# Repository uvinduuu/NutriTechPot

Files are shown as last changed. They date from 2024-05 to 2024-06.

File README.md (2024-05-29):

# NutriTechPot

**EN - 1190 ENGINEERING DESIGN PROJECT**

---

## Table of Contents
1. [Problem Description and Motivation](#problem-description-and-motivation)
2. [Product Idea Validation](#product-idea-validation)
3. [Technical Feasibility](#technical-feasibility)
4. [Product Architecture](#product-architecture)
5. [Changes We Made](#changes-we-made)
6. [Designs](#designs)
7. [Marketing and Sales](#marketing-and-sales)
8. [Future Improvements](#future-improvements)
9. [Power Consumption and Battery Life](#power-consumption-and-battery-life)
10. [Project Budget](#project-budget)
11. [Contact](#contact)

---

## Problem Description and Motivation

### Problem Description
Many people struggle with keeping their plants alive due to inconsistent watering and inadequate sunlight. For busy individuals or those without a green thumb, this can be a frustrating and costly problem. Our project aims to address this issue by creating a smart plant pot that automatically waters plants when the soil moisture level is low to ensure optimal growing conditions. By providing a solution to this common problem, we hope to make plant care more accessible and enjoyable for everyone.

### Motivation
The motivation for selecting the smart plant pot project was driven by the growing trend of agriculture-based products in the world. With an increasing focus on sustainability and healthy living, more people are turning to plant care as a way to connect with nature and improve their indoor air quality. By creating a smart plant pot that automates watering, we aim to make plant care more accessible and enjoyable for everyone. Furthermore, with the rising interest in smart home technology, we believe that our product has the potential to tap into a large and growing market.

---

## Product Idea Validation
We conducted a survey among a randomly selected group of about 50 people to validate the product idea for our smart plant pot. The survey revealed that a majority of participants struggled with plant care due to inconsistent watering and providing fertilization. Most people stated that they liked gardening but didn't have enough time to look after plants, and they often forgot to water them. Over 70% of respondents expressed interest in using a smart plant pot that automatically waters their plants. Participants also identified features such as automatic watering and real-time monitoring as desirable in a smart plant pot. Based on the survey results, we believe that our smart plant pot has promising market potential and addresses a common pain point among plant enthusiasts.

---

## Technical Feasibility
The product is designed to automatically water plants when the soil moisture level is low for optimal plant growth. To achieve this, we will use hardware components such as the Atmega328p microcontroller, capacitive soil moisture sensor, DC water pump, and a water level detector. All necessary components are readily available. Software requirements include the Arduino IDE for programming the microcontroller, Android Studio for app development, Altium Designer for PCB design, and Solidworks for enclosure design. We plan to hire professionals for PCB printing and 3D printing. The necessary resources, including soldering equipment, are available.

---

## Product Architecture

- **Power Supply**
- **Soil Moisture Sensor**
- **Atmega 328p Microcontroller**
- **DC Water Pump**
- **Water Level Sensor**
- **Bluetooth Module**
- **NutriTech App**

The NutriTech application tracks the water level in the tank, alerts the user when a refill is needed, and constantly monitors the soil moisture level, presenting the data in an easily understandable format to the user.

---

## Changes We Made
Initially, we planned to use a Wi-Fi module (ESP 8266) for communication between the chip and the NutriTech Pot application. However, we encountered significant challenges with this approach, such as needing to modify the code every time the pot was moved to a different Wi-Fi network. We switched to using a Bluetooth module (HC-05), which offers higher accuracy and a more user-friendly experience. This change enhanced the overall functionality and user experience of the NutriTech Pot application.

---

## Designs

### Schematic Diagram
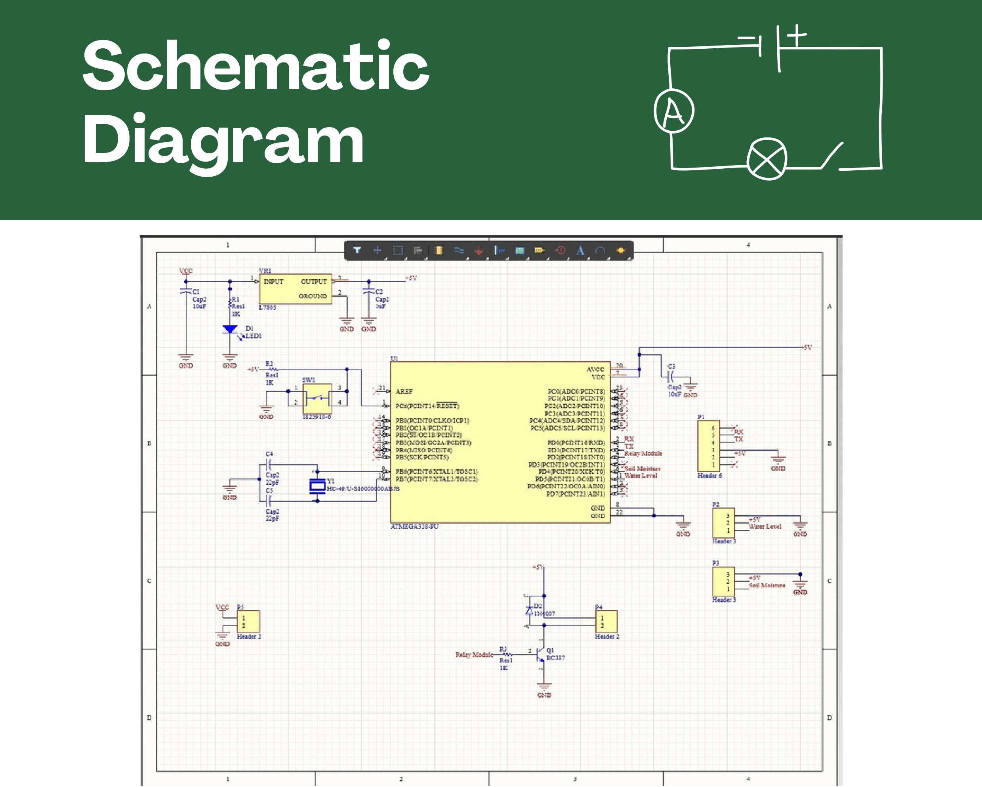
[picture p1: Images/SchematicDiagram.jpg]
Schematic Diagram


### NutriTech Pot App
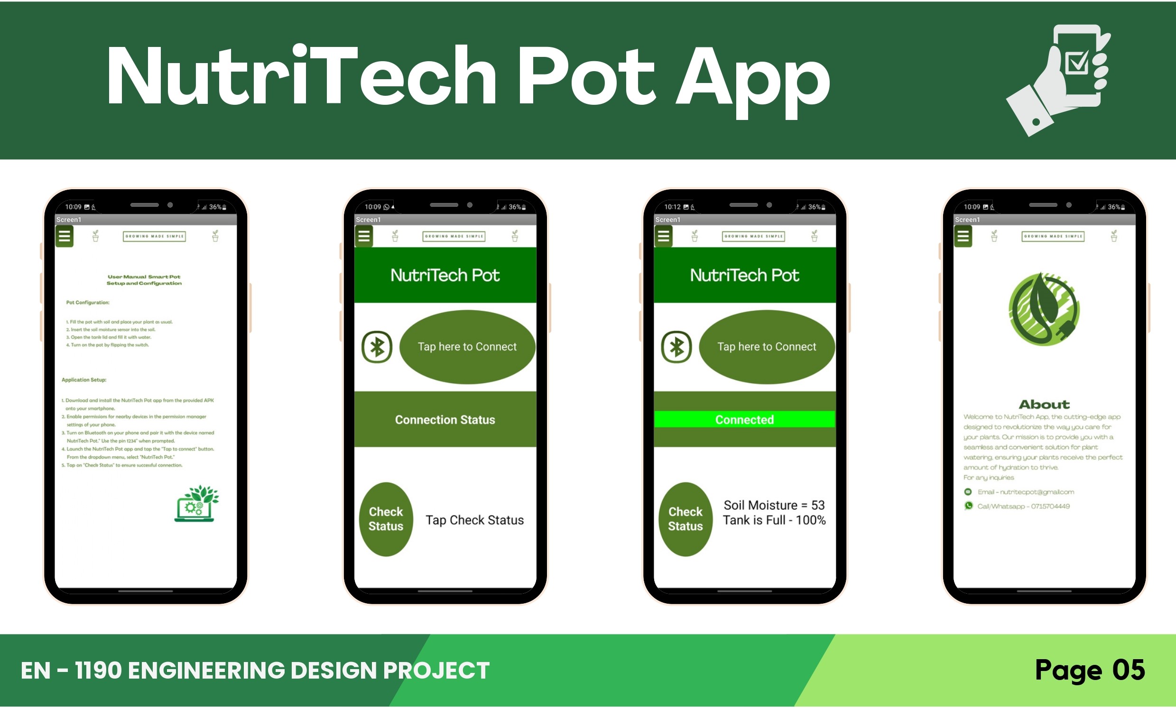
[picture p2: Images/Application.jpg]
NutriTech Pot App


### Altium Design
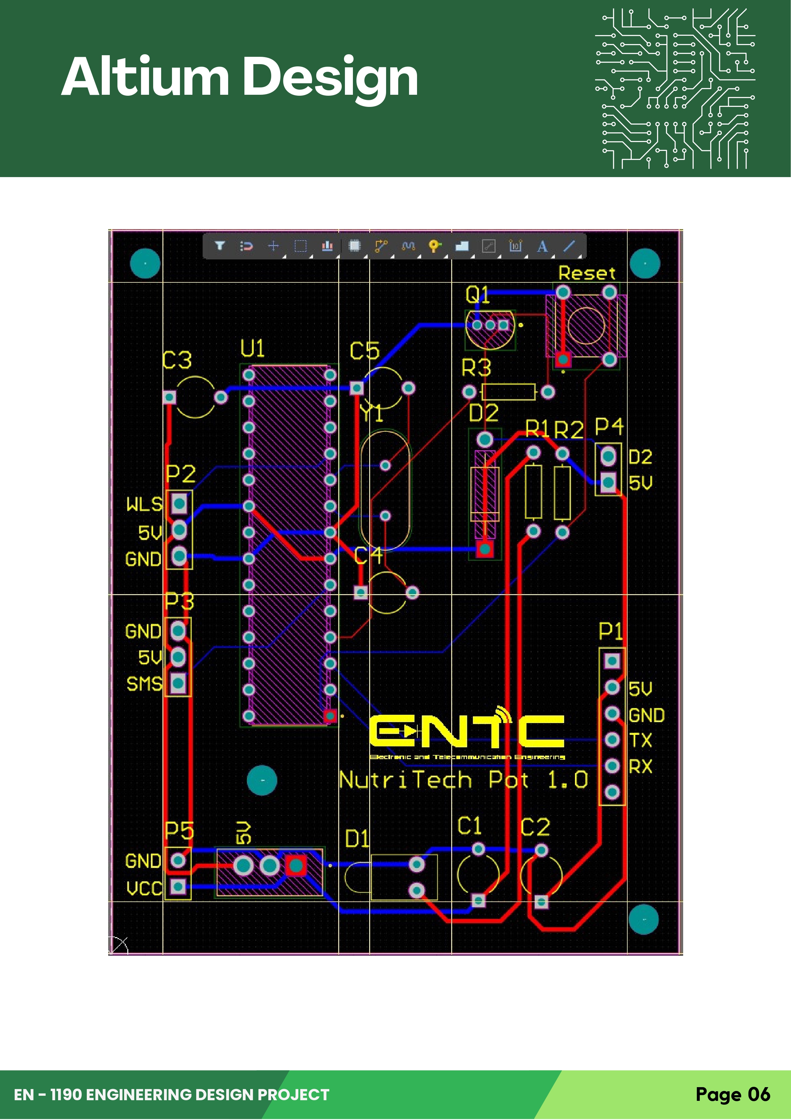
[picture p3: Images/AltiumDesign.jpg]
Altium Design


### Final Enclosure
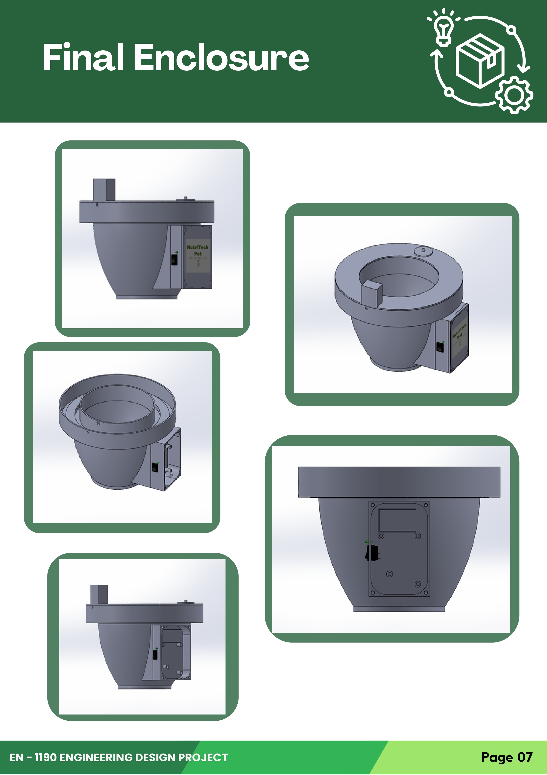
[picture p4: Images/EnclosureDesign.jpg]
Final Enclosure


---

## Marketing and Sales

### Competitive Forces
The market is new and growing, with evolving competition. Product quality, pricing, support, and marketing affect competitive forces. Intensified competition and tech advancements require staying ahead.

### Marketing Strategies
- **Social Media Marketing**
- **Influencer Marketing**
- **Email Marketing**
- **Content Marketing**

### Target Markets
Our project targets people who care about gardening and sustainability, especially those living in urban areas with limited outdoor space or who are too busy to take care of plants manually. We plan to market the product to them by emphasizing its convenience and benefits.

### Product Packaging
The product packaging will be made of recycled materials and have eco-friendly messaging and imagery. It will also be sturdy and protective to keep the product safe during transport.

### Warranty Terms
We offer a 6-month warranty period with a 10-month service period for the smart watering and fertilizing pot, covering any defects in materials or workmanship. The warranty period is clearly communicated to customers, and any necessary steps for claiming warranty are made easily accessible.

### After Sales Service
We provide clear instructions for cleaning and upkeep to ensure the product lasts for a long time. Additionally, we offer repair services for any damages or malfunctions that occur during the warranty and service period.

### Reuse/Recycle and Disposal
We encourage customers to reuse and recycle the product when it is no longer needed. The product is designed to be easily disassembled and recyclable at the end of its life cycle. We also plan to offer recycling programs or incentives for customers who choose to recycle the product.

### Sales Channels
- **Online Marketplaces:** Daraz, Ikman.lk, eBay
- **E-Commerce Website**
- **Retail Stores:** Collaborations with retail stores

---

## Future Improvements

### Bottlenecks of the Initial Plan
We initially powered the circuit using a 9V battery with a voltage regulator (L7805). However, the motor's high power draw caused the circuit to power down intermittently.

### Solution
We implemented two separate voltage regulators (L7805) – one for the Atmega chip's power supply and another for the DC water pump. We replaced the 9V battery with two rechargeable Li-ion batteries (3.7V Li-Fe 18650) for improved performance and stability. This ensured a consistent power supply to both the chip and the motor.

---

## Power Consumption and Battery Life
Through testing with a DC power supply, we measured the circuit's current draw when the motor was on at 160-170 mA and when the motor was off at 68-75 mA. We calculated an approximate power consumption of 1730mAh, providing nearly two and a half days of battery life on a single recharge. We used two rechargeable Li-ion batteries (3.7V Li-Fe 18650) connected in series due to the rapid discharge of the 9V battery.

---

## Project Budget

| Component | Qty | Unit Price (LKR) | Total Price (LKR) |
| --- | --- | --- | --- |
| Atmega328p Microcontroller | 1 | 1400.00 | 1400.00 |
| Capacitive Soil Moisture sensor | 1 | 400.00 | 400.00 |
| HC-05 Bluetooth Module | 1 | 1100.00 | 1100.00 |
| DC Water Pump | 1 | 380.00 | 380.00 |
| Li-ion batteries (3.7V Li-Fe 18650)| 2 | 600.00 | 1200.00 |
| Water Level Detector | 1 | 110.00 | 110.00 |
| 16MHz Crystal Oscillator | 1 | 40.00 | 40.00 |
| Resistors (1 kOhm - 1, 10 kOhm - 1)| 2 | 3.00 | 6.00 |
| BC 337 npn Transistor | 1 | 5.00 | 5.00 |
| IN 4007 Diode | 1 | 5.00 | 5.00 |
| Push Button Switch | 1 | 30.00 | 30.00 |
| Voltage Regulator | 2 | 50.00 | 100.00 |
| Capacitors | 5 | 5.00 | 25.00 |
| Connectors | 6 | 20.00 | 120.00 |
| LED | 2 | 15.00 | 30.00 |
| **Total** | | | **4951.00** |

### Total Production Cost
- Rs 3000 (For multiple product manufacturing)
- PCB Printing and 3D Printing - Rs 200 (per unit)
- Market Price - Rs 3600
- Manufacturing Quantities - 50 units

---
## Contact

For more information about the NutriTech Pot, contact us:

- Email: uvindukodikara@gmail.com
---

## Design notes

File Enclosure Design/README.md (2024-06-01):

# NutriTech Pot Enclosure

Welcome to the NutriTech Pot Enclosure repository! This repository contains the design files for the enclosure of the NutriTech Pot, a smart plant pot with an automatic watering system. Currently, we have designed and printed the PCB housing box, which will be the first step towards the full product.



## Features

- **Simple Box Design**: The enclosure is a straightforward, easy-to-assemble box with a lid.
- **PCB Mounting**: The PCB can be securely fixed inside the box using M3 screws.
- **Battery Compartment**: The enclosure has space to fit a 9V battery.
- **Power Control**: Equipped with a rocker switch to turn the power on and off.
- **Power Indicator**: Includes an LED to indicate the power status.

## Dimensions

- **Box Size**: 120 mm x 70 mm

## Usage

1. **Print the Box**: Use the provided SolidWorks files to 3D print the enclosure.
2. **Mount the PCB**: Fix the PCB inside the box using M3 screws.
3. **Install the Battery**: Place a 9V battery in the designated compartment.
4. **Connect the Rocker Switch and LED**: Wire the rocker switch and LED as indicated to control and show the power status.

## Future Plans

Originally designed with an inbuilt water tank, the NutriTech Pot will eventually include a complete system for automatic watering. This initial enclosure is just for the PCB and power components.

WhatsApp Image 2024-05-16 at 10 39 33_1c1a7363

## Contact

For any questions or inquiries, please contact [mihiruth@gmail.com](mailto:mihiruth@gmail.com).

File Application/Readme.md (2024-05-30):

# Nutritech Pot Application

Nutritech Pot is a smart watering system designed to help you maintain optimal soil moisture levels for your plants. This application, built using MIT App Inventor, connects to your Nutritech Pot via Bluetooth and provides real-time monitoring and alerts.

## Features

- **Bluetooth Connectivity**: Connect to your Nutritech Pot using Bluetooth to start monitoring.
- **Real-time Soil Moisture Level**: View the current soil moisture level as a percentage.
- **Water Tank Level**: Check the water tank level as a percentage.
- **Refill Alerts**: Receive notifications when it's time to refill the water tank.

## Getting Started

1. **Connect via Bluetooth**: Open the app and connect to your Nutritech Pot device via Bluetooth.
2. **Monitor Levels**: Once connected, the app will display real-time soil moisture and water tank levels.
3. **Refill Alerts**: The app will alert you when the water tank needs refilling.

## Requirements

- An Android device with Bluetooth capability.
- Nutritech Pot hardware.

## Installation

1. Download the Nutritech Pot APK from the release section.
2. Install the APK on your Android device.
3. Open the app and pair it with your Nutritech Pot device via Bluetooth.

## Usage

1. Open the app and navigate to the Bluetooth connection screen.
2. Select your Nutritech Pot device from the list of available devices.
3. Monitor the soil moisture level and water tank level displayed on the main screen.
4. Refill the water tank when you receive an alert.

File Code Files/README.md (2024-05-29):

# Soil Moisture and Water Level Monitoring System

## Features:

- **Soil Moisture Measurement**: The `measureSoilMoisture` function reads the soil moisture level and maps it to a percentage.
- **Water Level Measurement**: The `measureWaterLevel` function reads the water level and turns on an LED if the level is below a certain threshold.
- **Water Pump Control**: The `controlWaterPump` function turns the water pump on or off based on soil moisture and water level.
- **Bluetooth Communication**: The `sendBluetoothData` function sends the soil moisture and water level data to a mobile application via an HC-05 Bluetooth module.

## Setup Instructions:

1. **Hardware Connections**:
   - Connect the soil moisture sensor to the analog pin A3.
   - Connect the water pump to pin A5.
   - Connect the water level sensor to analog pin A1.
   - Connect an LED to pin 13 for low water level indication.
   - Connect the HC-05 Bluetooth module to pins 2 (RX) and 3 (TX).

2. **Calibration Values**:
   - Adjust the `OpenAirReading` and `WaterReading` values in the code based on your soil moisture sensor's calibration.
   - Adjust the `WATER_LEVEL_THRESHOLD` value based on your water level sensor's calibration.

3. **Thresholds**:
   - Set the desired soil moisture threshold (`MOISTURE_THRESHOLD`) to control the water pump.

4. **Software Configuration**:
   - Ensure the correct pins are defined in the code.
   - Upload the provided Arduino sketch to your Arduino board.

5. **Bluetooth Communication**:
   - Pair the HC-05 Bluetooth module with your mobile application.
   - The soil moisture and water level data will be sent as a percentage to the connected mobile application.
   - If the water level is low, the message will include a refill alert.

## Notes:

- Adjust pin numbers, calibration values, and thresholds according to your specific setup and sensor calibration.
- Ensure proper power supply connections for the sensors and modules.
- The delay between measurements and data transmission is set to 1 second. Adjust this as needed for your application.

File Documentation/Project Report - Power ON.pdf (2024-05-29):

## EN - 1190 ENGINEERING DESIGN PROJECT

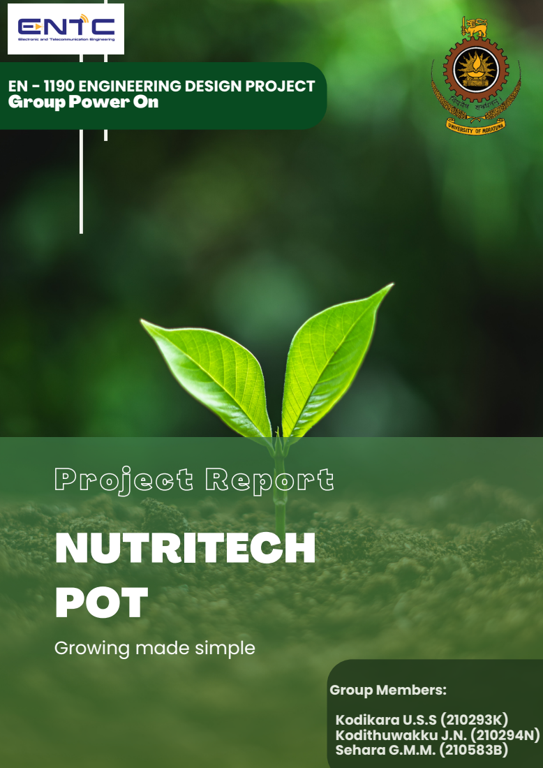
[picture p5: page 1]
Group Members:; Kodikara U.S.S (210293K) Kodithuwakku J.N. (210294N) Sehara G.M.M. (210583B); NUTRITECH POT; Project Report

Group Power On

Growing made simple

# Table of Contents

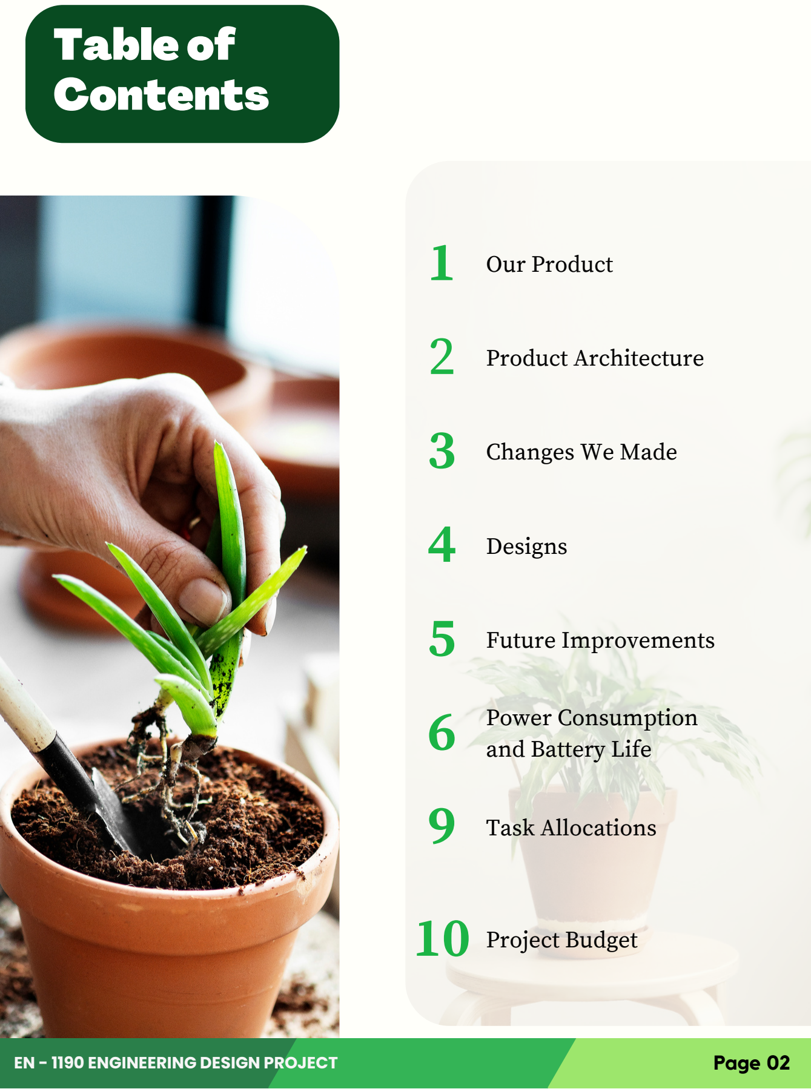
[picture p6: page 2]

## 1 Our Product

## 2 Product Architecture

## 3 Changes We Made

## 4 Designs

## 5 Future Improvements

6

## Power Consumption and Battery Life

## 9 Task Allocations

## 10 Project Budget

EN - 1190 ENGINEERING DESIGN PROJECT | Page 02

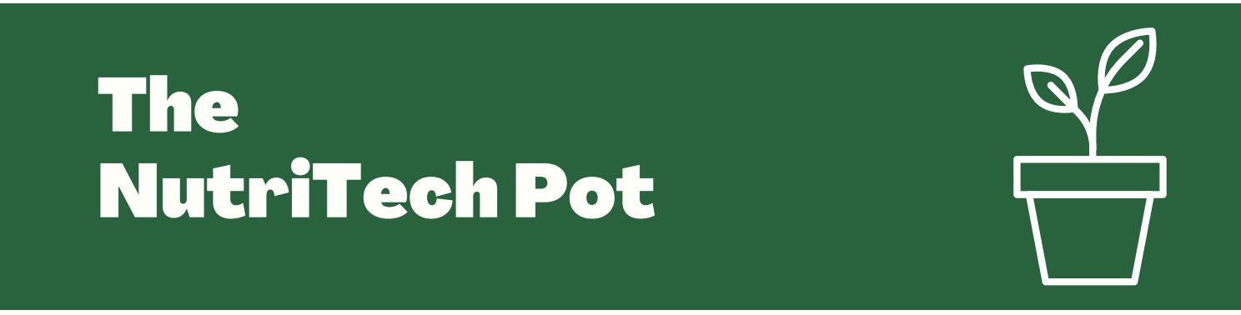
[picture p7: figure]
The NutriTech Pot
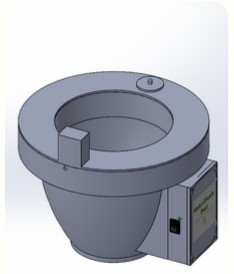
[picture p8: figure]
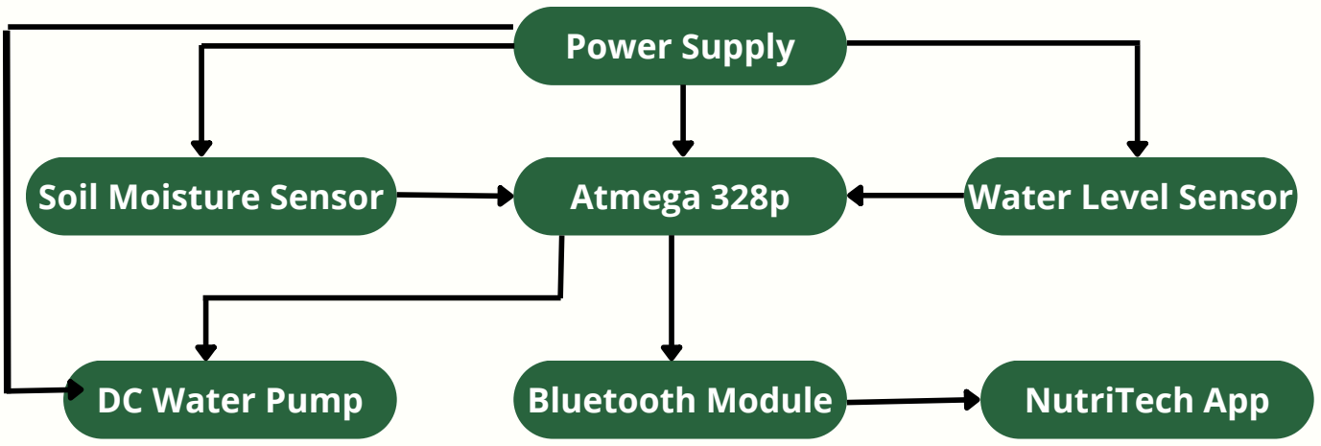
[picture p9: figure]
Power Supply; Soil Moisture Sensor; Atmega 328p; DC Water Pump; Water Level Sensor; Bluetooth Module; NutriTech App

EN - 1190 ENGINEERING DESIGN PROJECT | Page 03

The project aims to address the issues of plant watering by creating a smart plant pot that automatically waters plants when the soil moisture level is low to ensure optimal growing conditions.

The purpose of our product, the NutriTech pot, is to make gardening easier and more convenient for individuals who are interested in sustainable living but may not have access to outdoor gardening spaces or have busy lifestyles.
The pot is equipped with a soil moisture sensor and a water pump that automatically waters the plant when the soil moisture level is low. It also includes a water level detector that measures the water level in the tank and alerts the user when to add water.

## Product Architechture

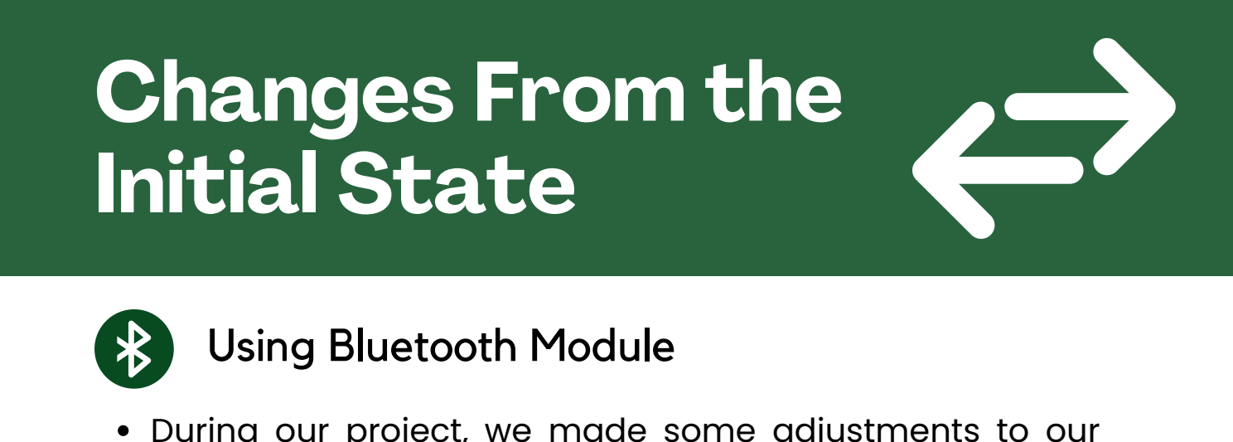
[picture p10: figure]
Studio Shodwe; Changes From the Initial State; Using Bluetooth Module
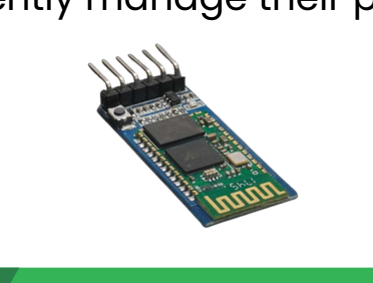
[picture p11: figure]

EN - 1190 ENGINEERING DESIGN PROJECT | Page 04

## During our project, we made some adjustments to our initial plan. Initially, we intended to employ a Wi-Fi module (esp 8266) for communication between the chip

and the NutriTech pot application.

## However, during the code development phase, we recognized a significant challenge with this approach. To

establish a connection between the app and the module,

## we needed to know the Network SSID and password of the Wi-Fi network which the module was meant to connect. This would have necessitated modifying the code every time the pot was moved to a different Wi-Fi

network, making it less practical for users.

## As a result, we sought an alternative solution and concluded that Bluetooth (HC-05) was a more suitable

option to establish the connection.

## Although Bluetooth has a shorter range compared to Wi-Fi, it offers higher accuracy and a more user-friendly experience. By using Bluetooth, we can seamlessly monitor the status of the pot and determine whether the tank requires a refill, as long as we are within a range of

approximately 10 meters from the pot.

This decision to switch to Bluetooth not only overcame the limitations of Wi-Fi but also enhanced the overall functionality and user experience of the NutriTech pot application. It allowed us to focus on delivering a more efficient and effective solution for our users, enabling them to conveniently manage their pot's watering needs

# Schematic Diagram

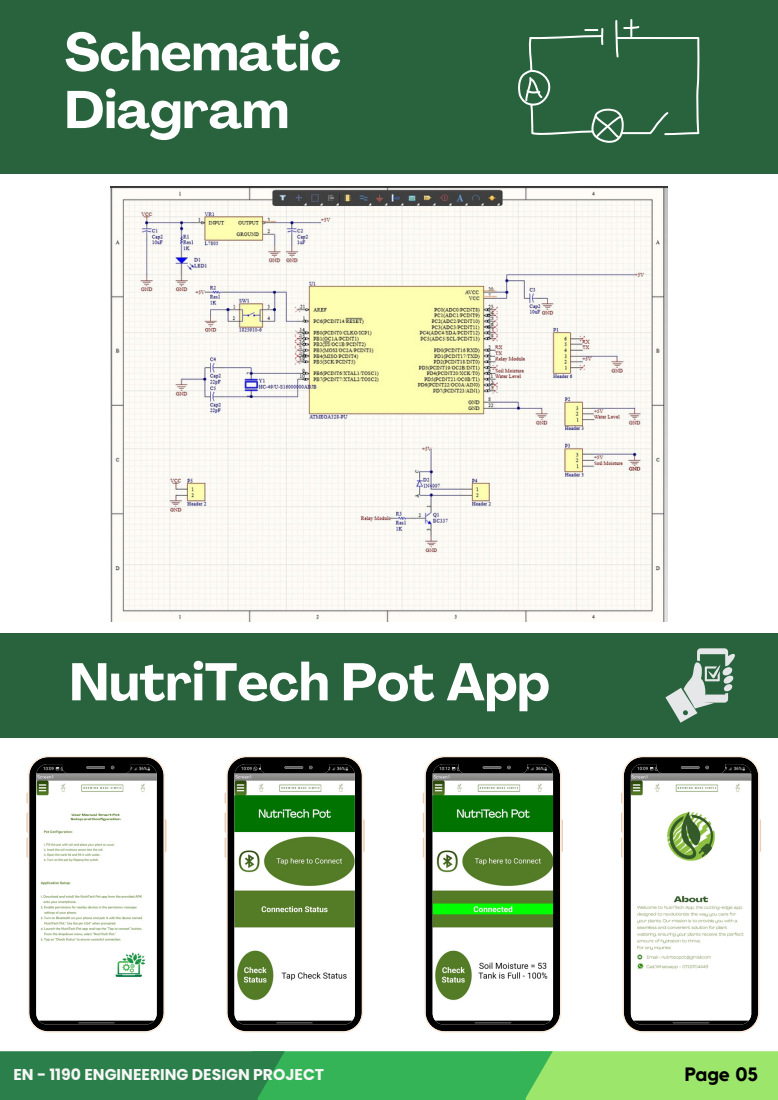
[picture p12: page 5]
Studio Shodwe; EN - 1190 ENGINEERING DESIGN PROJECT; Page 05

NutriTech Pot App

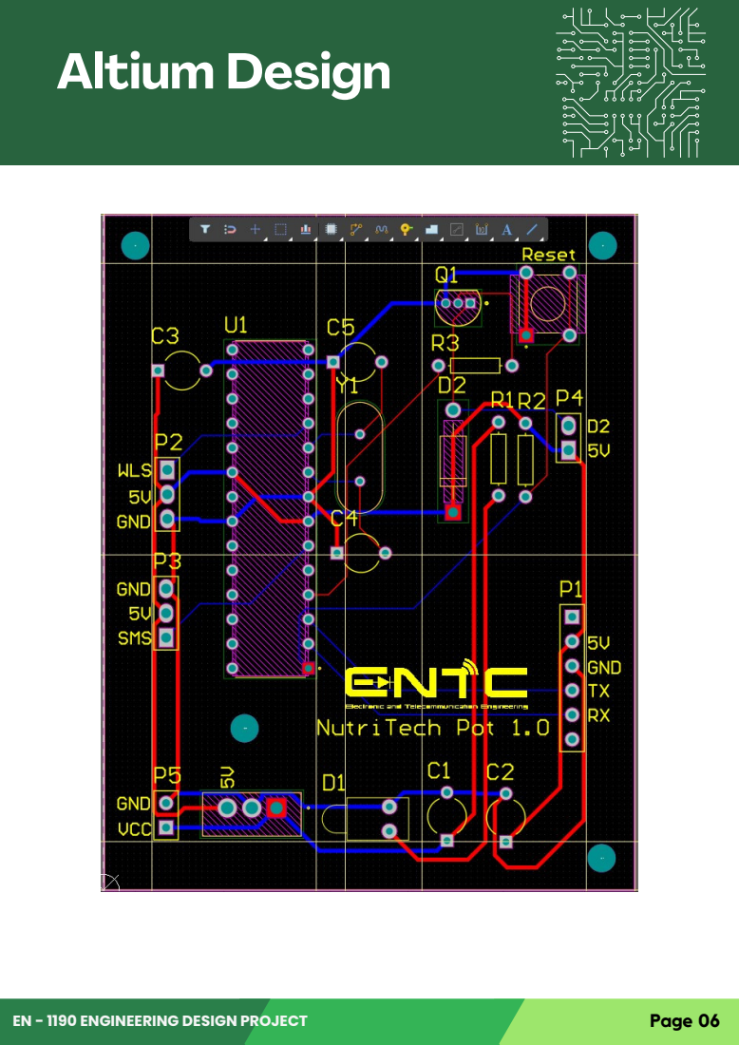
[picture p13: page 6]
AltiuSmtudio SDhodewesign; EN - 1190 ENGINEERING DESIGN PROJECT; Page 06

# FinalStEudionShcodwloe sure

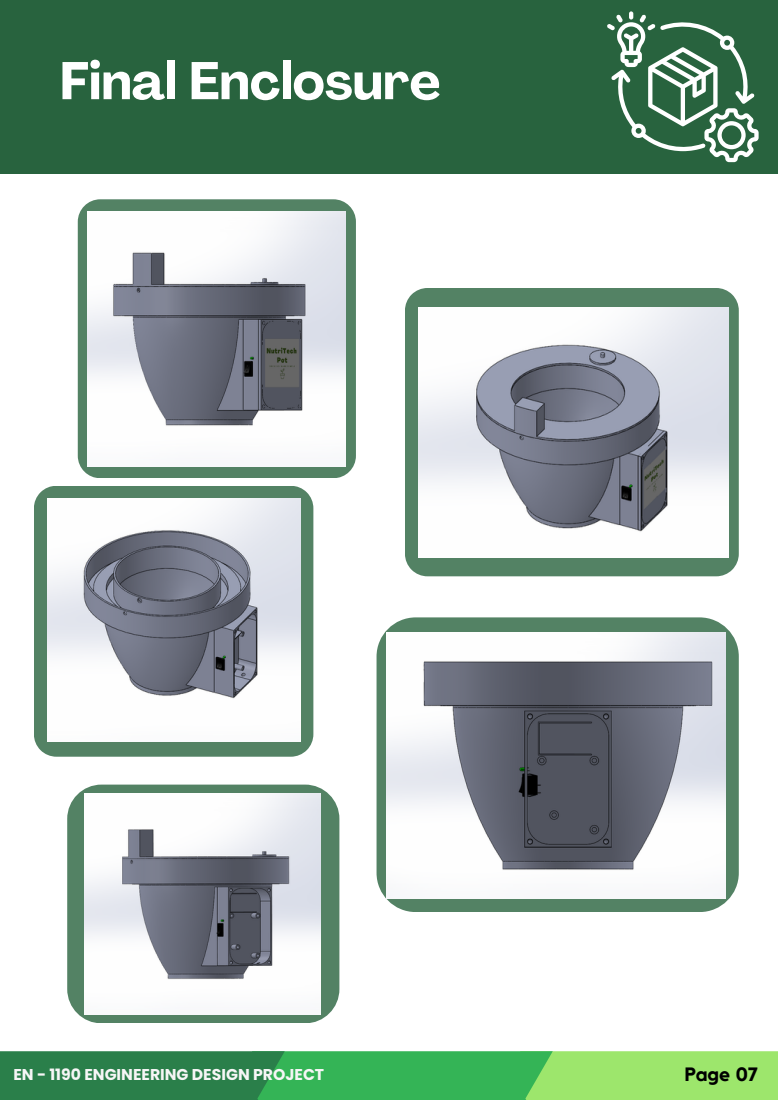
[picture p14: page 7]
EN - 1190 ENGINEERING DESIGN PROJECT; Page 07

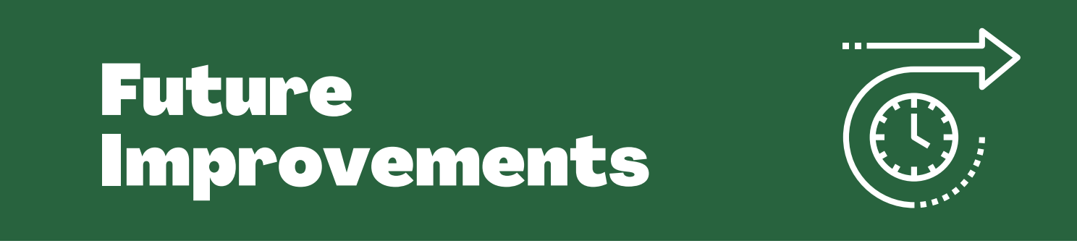
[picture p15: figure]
Future Improvements

B O T T L E N E C K S O F T H E I N I T I A L P L A N
In the project report, we initially planned to power the circuit using a 9V battery connected with a voltage regulator (L7805). However, during testing, we encountered a significant issue when the motor started to power up. The power LED began to blink, and the circuit powered down for a few seconds, repeating the same behavior.

We identified that the problem occurred because the motor drew a high amount of power from the circuit, which the power supply couldn't deliver. As a result, the voltage to the chip decreased, leading to the circuit's shutdown.

R E A S O N S

To address this issue, we devised a solution. We decided to implement two separate voltage regulators (L7805) – one for the atmega chip's power supply and another for the DC water pump. Additionally, we replaced the 9V battery with two rechargeable Li-ion batteries (3.7V Li-Fe 18650) as the new power supply for improved performance and stability. This modification allowed us to ensure a consistent power supply to both the chip and the motor, resolving the previous problem.

S O L U T I O N

D E M O N S T R A T I O N
For the demonstration, we utilized an LED instead of the DC water pump since it draws less current and effectively showcases the functionality of our product. Unfortunately, we couldn't alter the power supply in this instance due to the constraints of the enclosure and PCB, which were designed for the previously planned circuit.

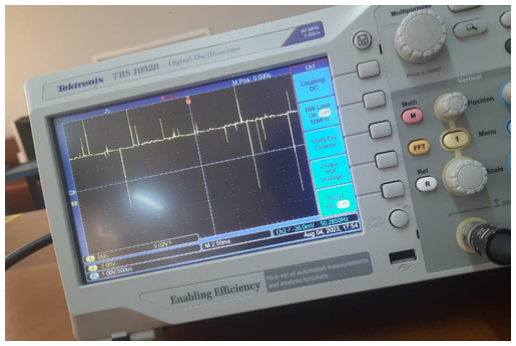
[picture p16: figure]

EN - 1190 ENGINEERING DESIGN PROJECT | Page 08 The photo shows an instance when the motor is connected to the circuit
with 9v battery.
| We can see a greater amount of
noise there

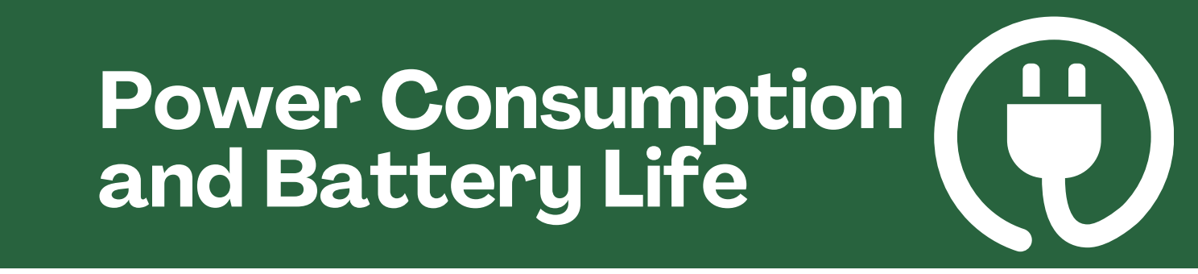
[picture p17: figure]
Power Consumption and Battery Life

EN - 1190 ENGINEERING DESIGN PROJECT | Page 09

Through testing with a DC power supply, we measured the circuit's current draw when the motor was on at 160-170 mA and when the motor was off at 68-75 mA.
Based on these observations, we calculated an approximate power consumption of 1730mAh, which would provide nearly two and a half days of battery life on a single recharge.
This estimation assumes a normal day with the
motor | activated | five | times | for | 15
seconds each time.

## Using two rechargeable Li-ion batteries (3.7V Li-Fe 18650) as the power supply

Due to the rapid discharge of the 9V battery, we
decided to use two 3.7V batteries connected in
series.

## Battery Life and Power Consumption

# Task Allocation

Kodikara K.S.S. - Microcontroller Programming and Mobile App Kodithuwakku J.N. - Altium and PCB Design
Sehara G.M.M. - Solidworks and Enclosure Design

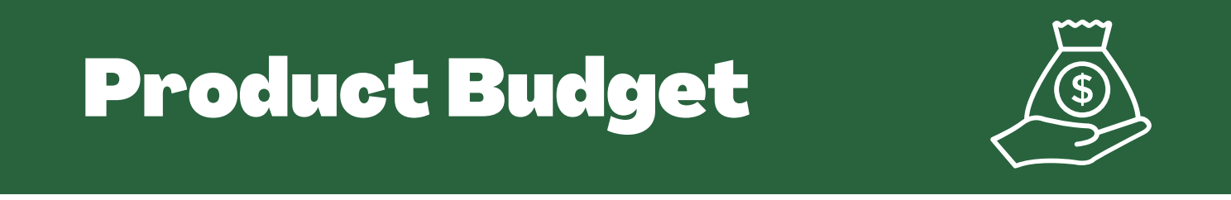
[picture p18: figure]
Product Budget

Component | Qty | Unit Price (LKR) | Price (LKR)
atmega328p Micro Controller | 1 | 1400.00 | 1400.00
Capacitive Soil Moisture sensor(MD0247) | 1 | 400.00 | 400.00
HC-05 Bluetooth Module | 1 | 1100 | 1100.00
DC water pump(RB0031) | 1 | 380.00 | 380.00
Li-ion batteries (3.7V Li-Fe 18650) | 2 | 600.00 | 1200.00
Water Level Detector(MD0207) | 1 | 110.00 | 110.00
16MHz Crystal Oscillator | 1 | 40.00 | 40.00
Resistors (1 kOhm - 1, 10 kOhm - 1) | 2 | 3.00 | 6.00
BC 337 npn Transistor | 1 | 5.00 | 5.00
IN 4007 Diode | 1 | 5.00 | 5.00
Push Button Switch | 1 | 30.00 | 30.00
Voltage Regulator | 2 | 50 | 100.00
Capacitors (10 micro F - 1, 22 pF - 2) | 5 | 5.00 | 25.00
Connectors | 6 | 20.00 | 120.00
LED | 2 | 15.00 | 30.00
Total | | | 4951.00
Total production cost | - Rs 4800(For multiple Product manufacturing)
PCB Printing and Injection Molding - Rs 1000 (per one unit)
Market Price | - Rs 7000
Manufacturing Quantities | - 50
EN - 1190 ENGINEERING DESIGN PROJECT | Page 10

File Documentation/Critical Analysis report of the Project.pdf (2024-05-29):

Critical Analysis report of the Project

NutriTech Pot: Team PowerOn

Kodikara U. S. S. – 210293K

Kodithuwakku J. N. – 210294N

Sehara G. M. M. – 210583B

Introduction:

Gardening has become a popular hobby among people, but not everyone has the time or expertise to provide their plants with the necessary care. As a solution to this issue, a smart pot that can detect and regulate water and fertilizer levels as required to maintain the plant's health is proposed. The idea is based on the application of deductive, inductive, and abductive reasoning to arrive at a practical and useful solution. This proposal aims to refine the idea further, including extended analysis of its technical, economic, and environmental aspects.

Deductive Reasoning:

Deductive reasoning entails using general observations to arrive at a specific conclusion. In the context of the proposed smart pot, the general observation is that many individuals enjoy gardening but do not have the time or expertise to give their plants the attention they require. As a result, a smart pot that can detect and regulate water and fertilizer levels as needed is suggested as a solution. To achieve this, the smart pot will include sensors to detect moisture levels, sunlight exposure, and fertilizer levels. The sensors will then send this data to an app that will regulate the water and fertilizer levels to keep the plant healthy. The smart pot will be beneficial for people who want to enjoy gardening but have time constraints, ensuring that their plants are well-cared for without requiring regular attention.

Inductive Reasoning:

Inductive reasoning involves drawing broad conclusions from specific observations. The observation in this context is that many individuals desire to engage in gardening activities but lack the time to care for their plants consistently. The smart pot's development is based on this observation and aims to give users a convenient way to keep an eye on their plants' health and regulate their water and fertilizer levels. The smart pot will help users to engage in gardening activities, enhancing their living space and providing a therapeutic outlet while requiring minimal effort.

Abductive Reasoning:

Abductive reasoning entails combining observations and imaginative thinking to arrive at a tenable solution. In this context, the observation is that many people are unable to care for their plants consistently due to time constraints. The solution proposed is a smart pot that can detect and regulate water and fertilizer levels as needed. The smart pot will also include a small tank filled with fertilizer liquid, which will release the necessary amount of fertilizer when the sensor detects a deficiency. The smart pot will also include a sunlight-measuring function to ensure that the plant is getting the necessary amount of light. The combination of these features will enable individuals to engage in gardening activities with minimal effort and ensure that their plants receive the care they require.

Extended Analysis:

The proposed smart pot has the potential to provide numerous benefits, including time-saving, convenience, and enhanced plant health. However, its efficacy, affordability, and environmental impact must be analyzed before its widespread use can be recommended.

Technical Analysis:

The technical analysis of the smart pot will include an assessment of its sensors, the app's effectiveness, and the device's durability. The sensors must be accurate and reliable to ensure that the plant receives the necessary care. The app must be user-friendly, and its data must be updated in real-time to provide timely information. The device must be durable and able to withstand the elements, ensuring that it can be used indoors or outdoors.

Economic Analysis:

The economic analysis will involve an assessment of the smart pot's cost-effectiveness, market demand, and profitability. The cost of the device must be affordable, allowing a wide range of individuals to access it. The market demand for the device must be sufficient to ensure its viability, and the device must be profitable to ensure its long-term sustainability.

Environmental Analysis:

The environmental impact of the smart pot must also be considered. The device must be made from environmentally sustainable materials, and its energy usage must be minimized to reduce its carbon footprint. The device must also be recyclable

Future Directions:

We plan to enhance the system by adding a charging module, which will eliminate the need for users to change batteries. Additionally, we will offer customized pots with unique designs for people in need.

Objectives: Our objectives for this project are as follows:

1. Incorporate a charging module into the pot to eliminate the need for users to change batteries.
2. Create customized pots with unique designs to meet the needs of different plants and customers.

Methodology: To achieve our objectives, we will follow the following methodology:

1. Integrate a charging module into the pot, which will use renewable energy sources to charge the battery and eliminate the need for users to change batteries.
2. Create customized pots with unique designs for different plants and customers, using 3D printing technology to produce them efficiently.

Expected Results: We expect the following results from our project:

1. A charging module that eliminates the need for users to change batteries and reduces maintenance costs.
2. Customized pots with unique designs that meet the needs of different plants and customers, providing an aesthetically pleasing and functional solution for indoor plant care.

Conclusion:

Our project aims to create a smart watering and fertilizing pot that is both functional and aesthetically pleasing, using sensors, microcontrollers, and 3D printing technology. By incorporating a charging module and offering customized designs, we aim to provide a user-friendly and sustainable solution for indoor plant care. We believe that this project has the potential to improve people's lives by promoting indoor plant growth, while also reducing the environmental impact of disposable batteries.

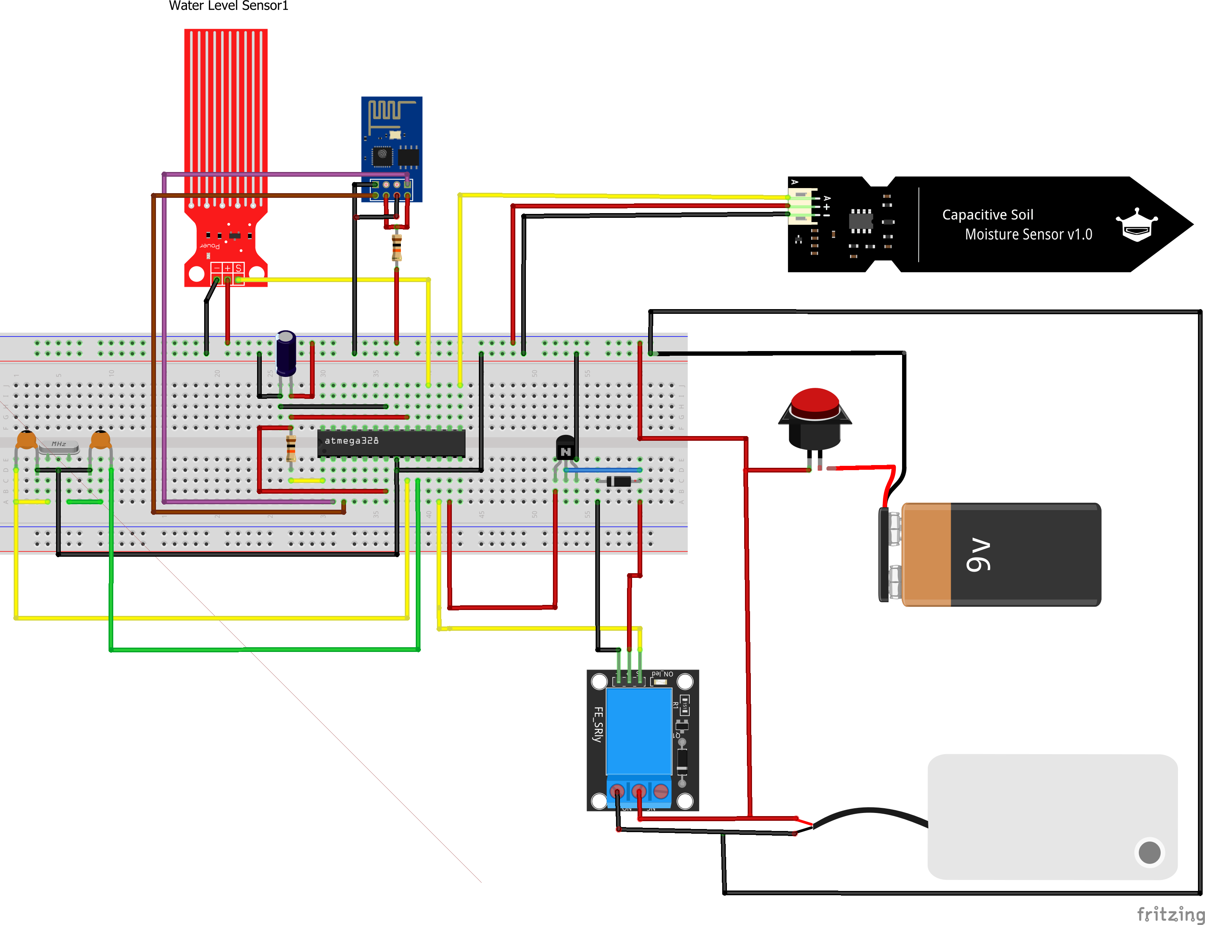
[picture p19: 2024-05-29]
PCB Design/Initial_Diagram.png

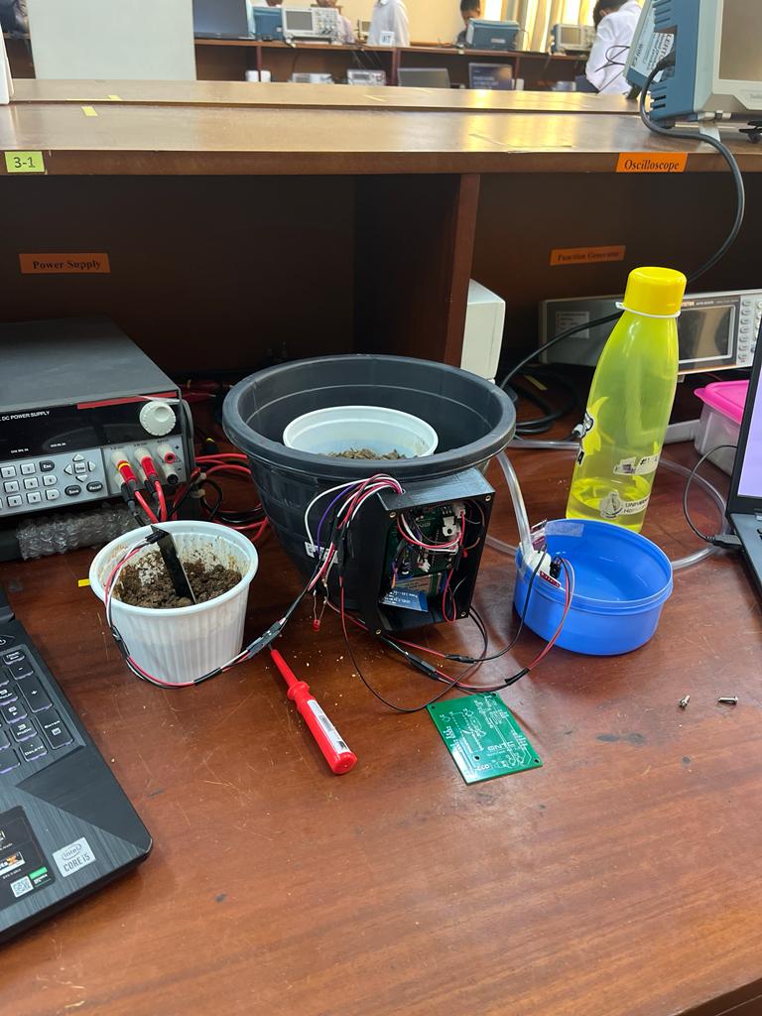
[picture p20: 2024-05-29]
Images/InnerView.jpg

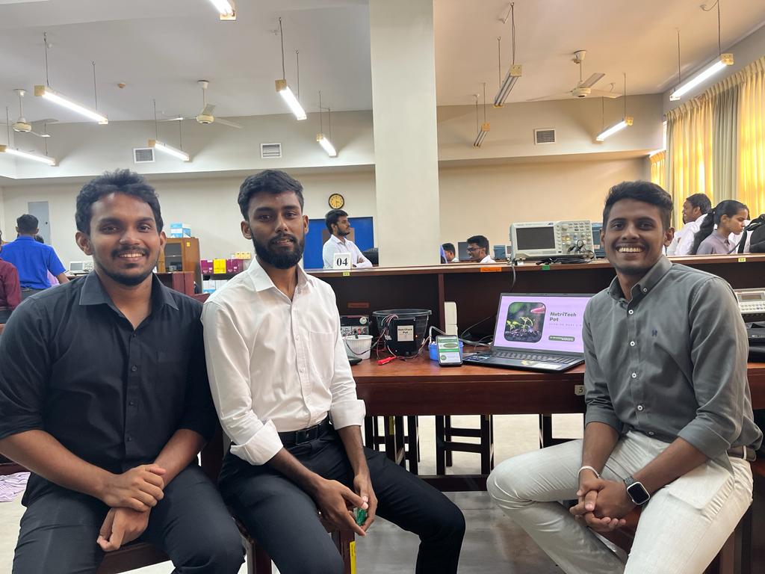
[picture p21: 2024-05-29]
Images/Team.jpg

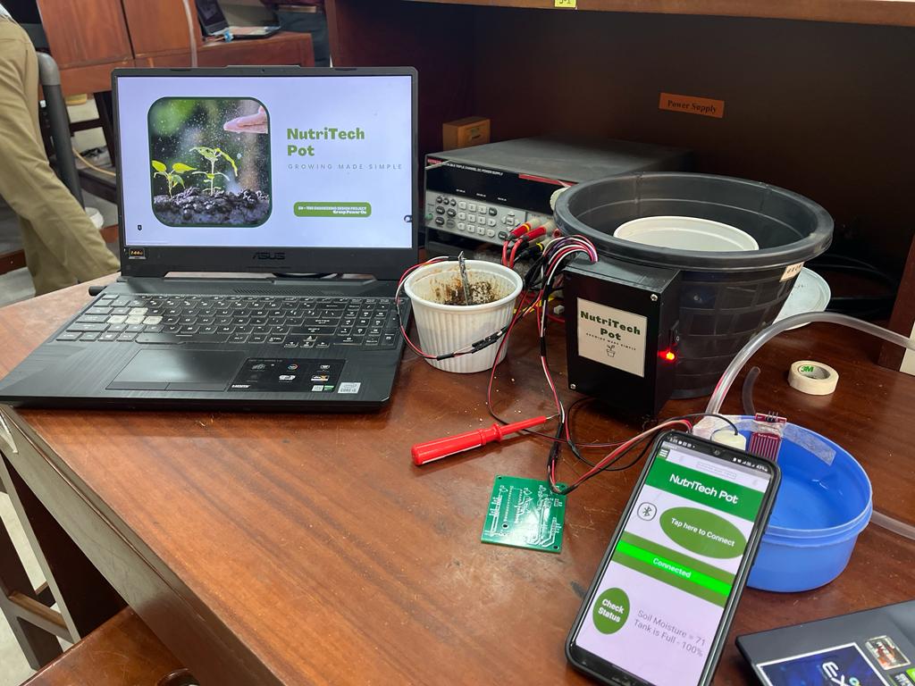
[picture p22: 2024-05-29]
Images/Demonstration.jpg

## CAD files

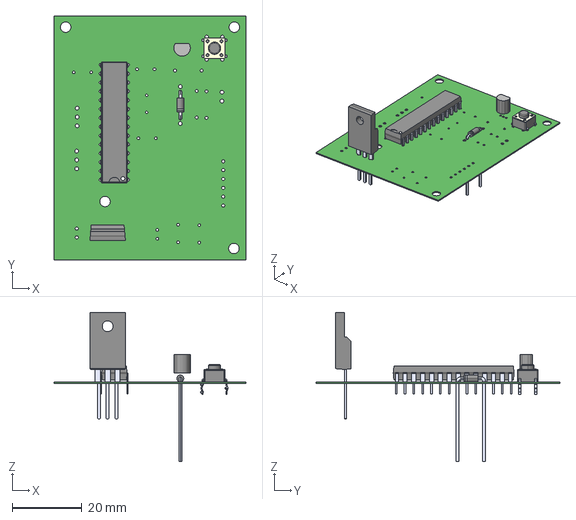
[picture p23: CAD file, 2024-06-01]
Enclosure Design/NutriTech PCB.step
55.0 x 70.0 x 42.9 mm

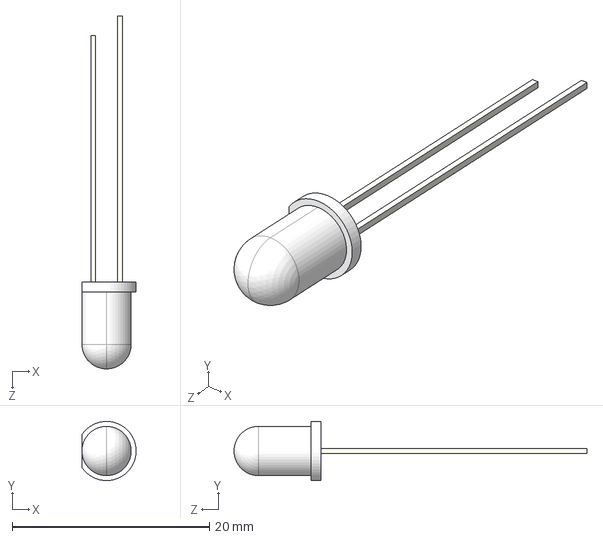
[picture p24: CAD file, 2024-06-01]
Enclosure Design/LED 5mm.STEP
5.49 x 6.00 x 35.8 mm

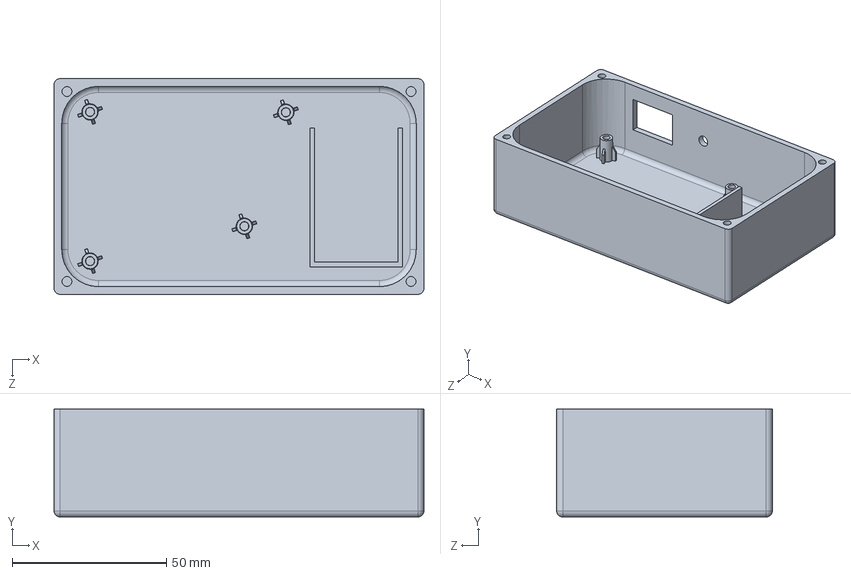
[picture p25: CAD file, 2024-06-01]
Enclosure Design/Box.SLDPRT
120.0 x 35.0 x 70.0 mm

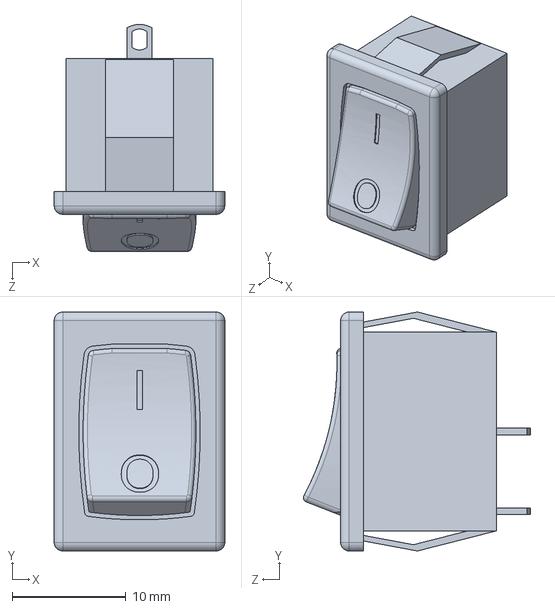
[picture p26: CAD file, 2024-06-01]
Enclosure Design/rocker switch 1.SLDPRT
15.0 x 21.0 x 20.0 mm

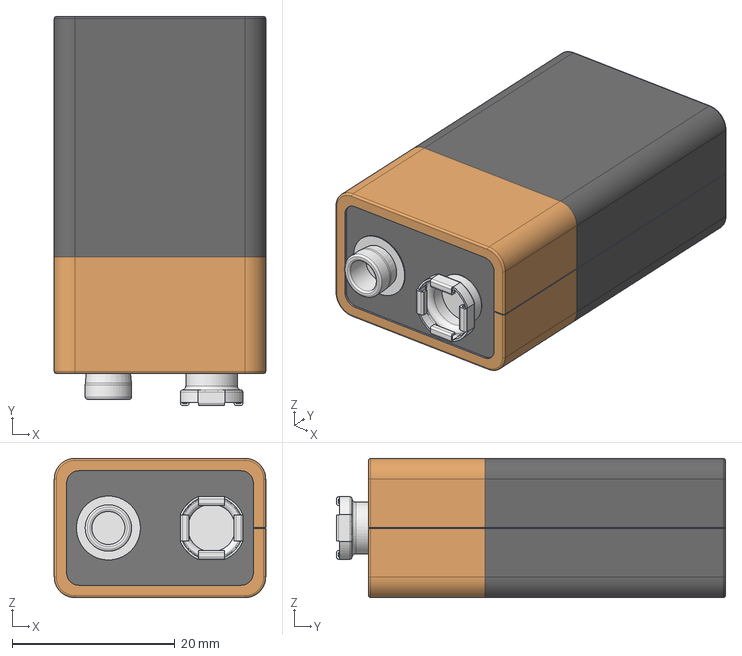
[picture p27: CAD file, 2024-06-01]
Enclosure Design/9V-battery.stp
26.0 x 47.9 x 17.1 mm

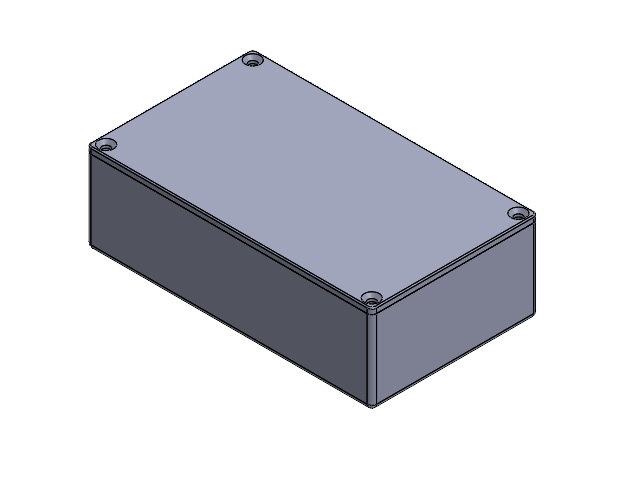
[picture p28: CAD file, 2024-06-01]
Enclosure Design/Assem1.SLDASM
NutriTech PCB.step
9V-battery.stp
Lid
rocker switch 1
LED 5mm.step

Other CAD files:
Enclosure Design/Lid.SLDPRT
Enclosure Design/NutriTech PCB.step.SLDPRT

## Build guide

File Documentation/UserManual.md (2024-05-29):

# Smart Pot Setup and Configuration

## Application Setup:
1. **Download and install the NutriTech Pot app:** Obtain the app from the provided APK and install it on your smartphone.
2. **Enable permissions for nearby devices:** Navigate to the permission manager settings of your phone and enable permissions for nearby devices.
3. **Turn on Bluetooth and pair with the device:** Enable Bluetooth on your phone and pair it with the device named "NutriTech Pot." Use the pin "1234" when prompted.
4. **Launch the NutriTech Pot app:** Open the app and tap the "Tap to connect" button. From the dropdown menu, select "NutriTech Pot."
5. **Check Status:** Tap on "Check Status" within the app to ensure successful connection.

## Pot Configuration:
1. **Fill the pot with soil:** Prepare the pot by filling it with soil and place your plant as usual.
2. **Insert soil moisture sensor:** Insert the soil moisture sensor into the soil.
3. **Fill the tank with water:** Open the tank lid and fill it with water.
4. **Turn on the pot:** Flip the switch to turn on the pot.
5. **Monitor pot's status:** Use the application to monitor the pot's status. Refill the tank as prompted by opening the lid and adding water when necessary.
6. **Check LED status:** Check the pot's LED status triweekly. If it's turned off, recharge the batteries.

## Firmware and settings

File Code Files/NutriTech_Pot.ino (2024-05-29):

#include <SoftwareSerial.h>

// Calibration constants for soil moisture sensor
const int OpenAirReading = 565;   // calibration data 1
const int WaterReading = 385;     // calibration data 2

// Pin definitions
const int MOTOR_PIN = A5;
const int POWER_PIN = 7;
const int SIGNAL_PIN = A3;
const int WATER_LEVEL_PIN = A1;   // Analog pin for water level sensor
const int LED_PIN = 13;           // LED pin for low water level indication

// HC-05 Bluetooth module pins
const int RX_PIN = 2;
const int TX_PIN = 3;

// Thresholds
const int MOISTURE_THRESHOLD = 50;
const int WATER_LEVEL_THRESHOLD = 300;  // Threshold for water level (adjust based on calibration)

// Global variables
int moistureLevel = 0;
int soilMoisturePercentage = 0;
int waterLevel = 0;
SoftwareSerial bluetooth(RX_PIN, TX_PIN);

void setup() {
  Serial.begin(9600);        // Start serial communication at 9600 bps
  bluetooth.begin(9600);     // Start Bluetooth communication at 9600 bps

  pinMode(MOTOR_PIN, OUTPUT);
  pinMode(POWER_PIN, OUTPUT);
  pinMode(LED_PIN, OUTPUT);

  digitalWrite(POWER_PIN, LOW); // Turn the sensor OFF initially
  digitalWrite(LED_PIN, LOW);   // Turn the LED OFF initially
}

void loop() {
  measureSoilMoisture();
  measureWaterLevel();
  controlWaterPump();
  sendBluetoothData();
  delay(1000);
}

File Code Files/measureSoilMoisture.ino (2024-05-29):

void measureSoilMoisture() {
  digitalWrite(POWER_PIN, HIGH);  // Turn the sensor ON
  delay(10);                      // Wait 10 milliseconds
  moistureLevel = analogRead(SIGNAL_PIN); // Read the analog value from sensor
  digitalWrite(POWER_PIN, LOW);   // Turn the sensor OFF

  soilMoisturePercentage = map(moistureLevel, OpenAirReading, WaterReading, 0, 100);
  
  if (soilMoisturePercentage >= 100) {
    Serial.println("\nMaximum - 100 %");
    soilMoisturePercentage = 100;
  } else if (soilMoisturePercentage <= 0) {
    Serial.println("\nMinimum - 0 %");
    soilMoisturePercentage = 0;
  } else {
    Serial.print(soilMoisturePercentage);
    Serial.println("%");
  }
}

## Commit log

2024-05-29 Create PCB Design
2024-05-29 Rename Project Proposal Gorup Power On.pdf to Final Project Report.pdf
2024-05-29 Rename Enclosure Design.jpg to EnclosureDesign.jpg
2024-05-29 Rename Schematic Diagram.jpg to SchematicDiagram.jpg
